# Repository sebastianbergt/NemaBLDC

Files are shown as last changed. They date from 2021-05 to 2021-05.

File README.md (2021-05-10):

# NemaBLDC

# Goal

Provide a Nema34 compatible case for C6374 170KV BLDC Motor with CUI AMT V102 encoder to be used as a powerful servo with [odrive](https://odriverobotics.com/).

# Pictures 

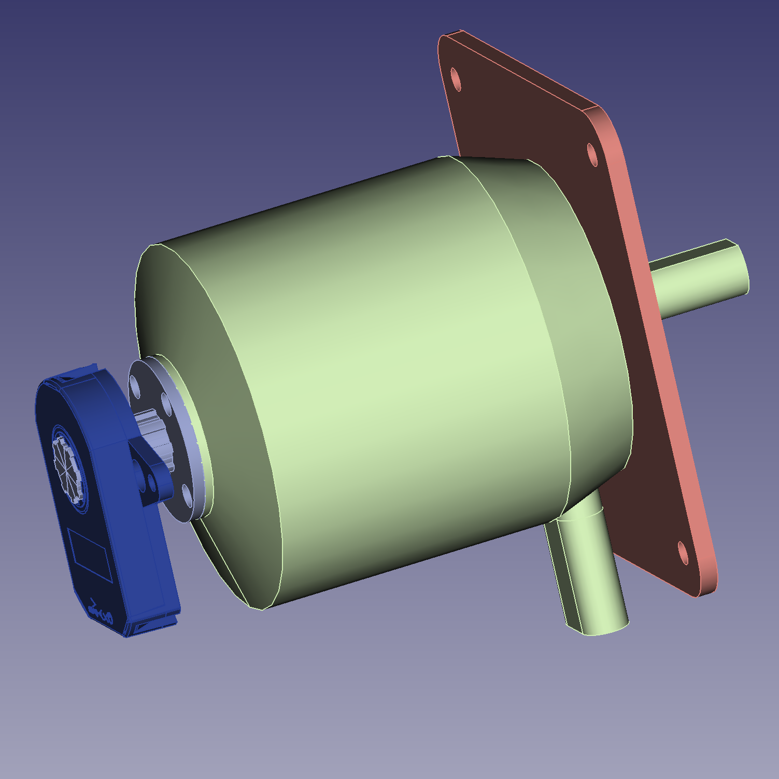
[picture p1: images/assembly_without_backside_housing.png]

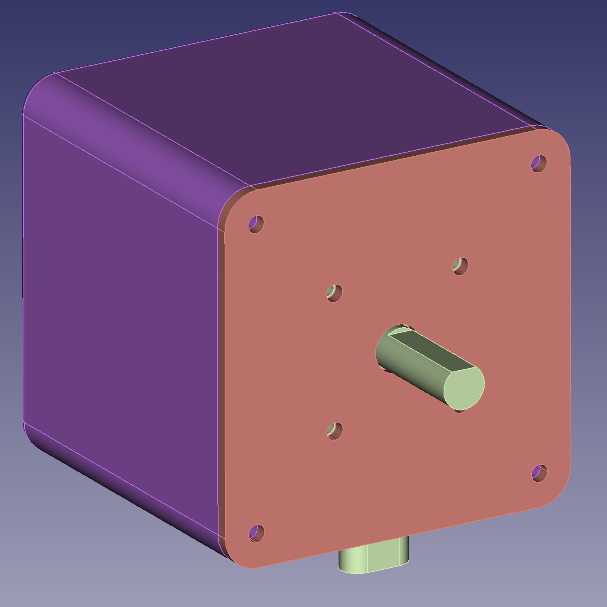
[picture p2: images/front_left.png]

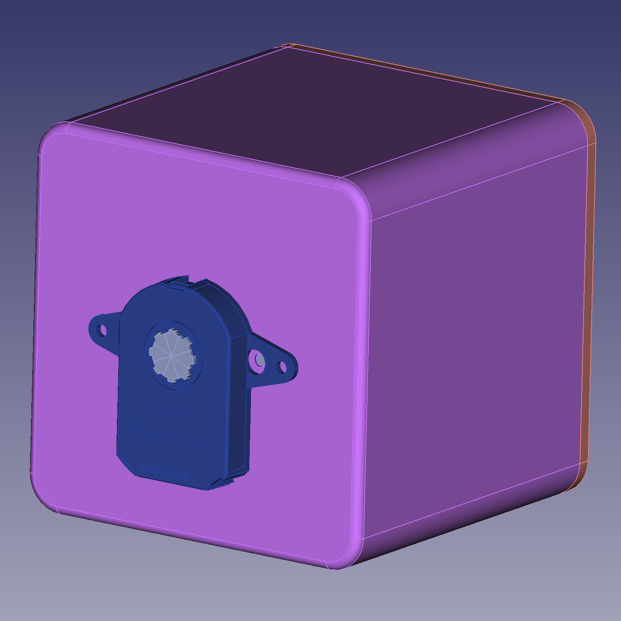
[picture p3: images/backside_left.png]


# Print

All parts were printed on [Prusa MK3S](https://www.prusa3d.com/) with PETG 0.15mm layer height and PrusaSlicer-2.2.0 default-QUALITY setting, 0.4mm nozzle as well as 2 perimeters without supports.
Back and front have 15% gyroid infill.
The encoder shaft has 100% rectolinear infill.
CAD were designed in freecad version 0.19 with Assembly 4 addon.

# Build

1. Clean the M4 nut slots as overhanging arches tend to produce a small amount of blocking material.
2. Insert M3 nuts and use tape or glue to hold them in place. 
3. Insert M4 nuts and use tape or glue to hold them in place.
4. Attach encoder mount, usually no need for using the mounting tool delivered with the encoder
5. Attach encoder and encoder cable
6. Attach encoder shaft to motor with 2 M4 screws
7. Attach motor to front plate with 4 M4 screws
8. Carefully insert motor into case, having the teeth of the encoder shaft visible to avoid damaging the shaft or the encoder.
9. Close the case with 4 M4 screws from the front.

# BOM

|Count |Part  | Comment
--- | --- | ---
|2|M3 nut|for the encoder mount
|2|M3 5mm screw|for the encoder mount
|4|M4 nut|
|10|M4 10mm screw|for motor and encoder shaft mounting and keeping the front on the box
|1|[AMT102-V](https://octopart.com/amt102-v-cui+devices-106233269)|
|1|[AMT102-V cable](https://octopart.com/search?q=CUI-3132-1FT&currency=USD&specs=0)|
|some|PETG filament|

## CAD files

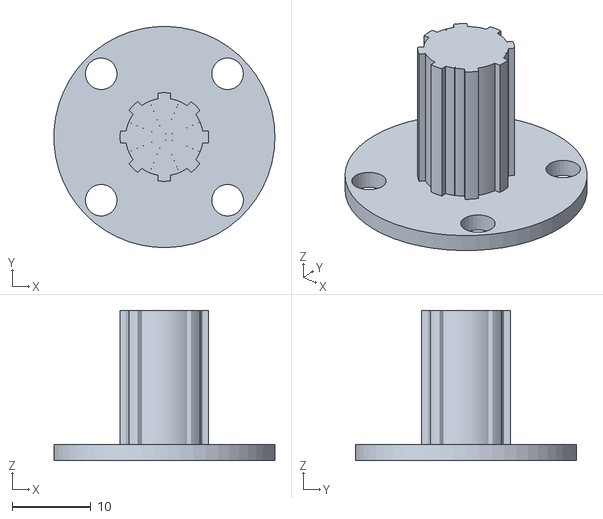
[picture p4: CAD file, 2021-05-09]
exports/Encoder_Shaft_Adapter-Encoder_Shaft_Adapter_v0.stl
28.0 x 28.0 x 19.0

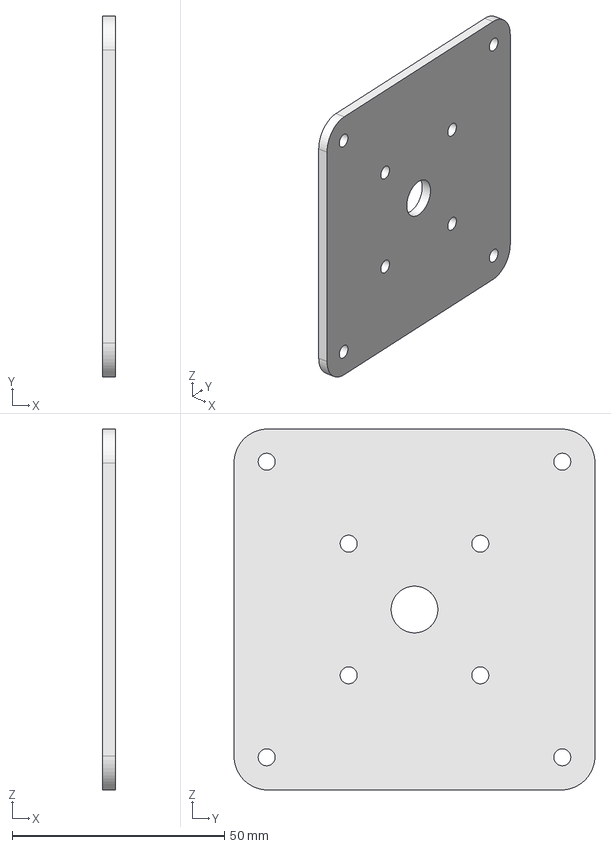
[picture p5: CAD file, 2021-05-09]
Motor_Housing_FrontPlate.FCStd
3.00 x 85.0 x 85.0 mm

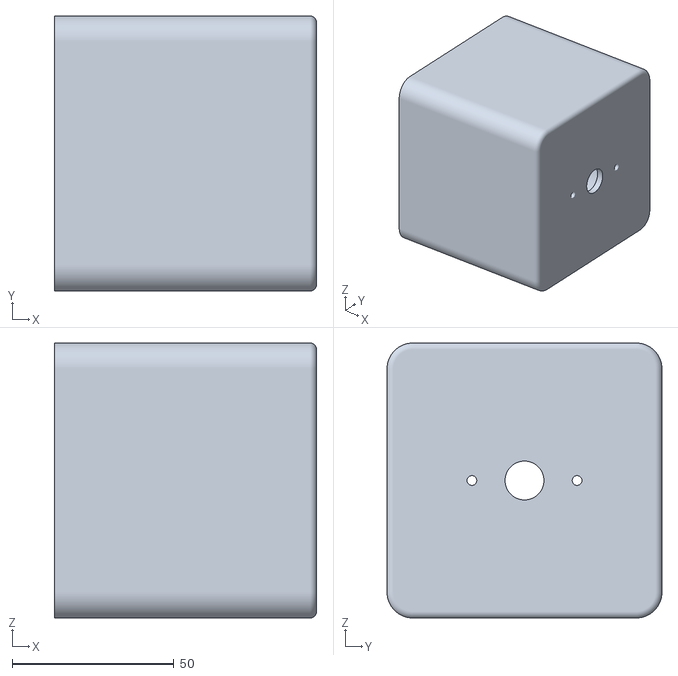
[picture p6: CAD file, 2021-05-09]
exports/Motor_Housing_Back-Motor_Housing_Back_v0.stl
81.0 x 85.0 x 85.0

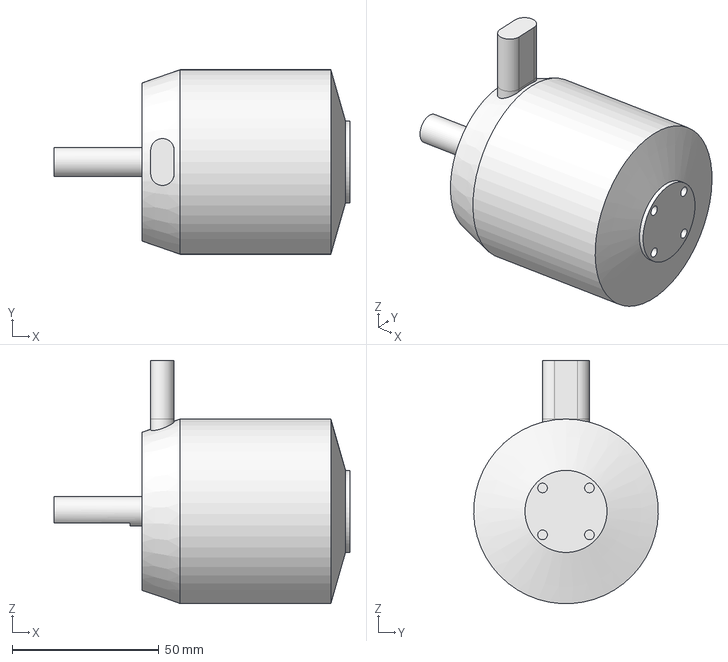
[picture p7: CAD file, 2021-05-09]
Motor_C6374_170KV.FCStd
101.0 x 63.0 x 82.9 mm

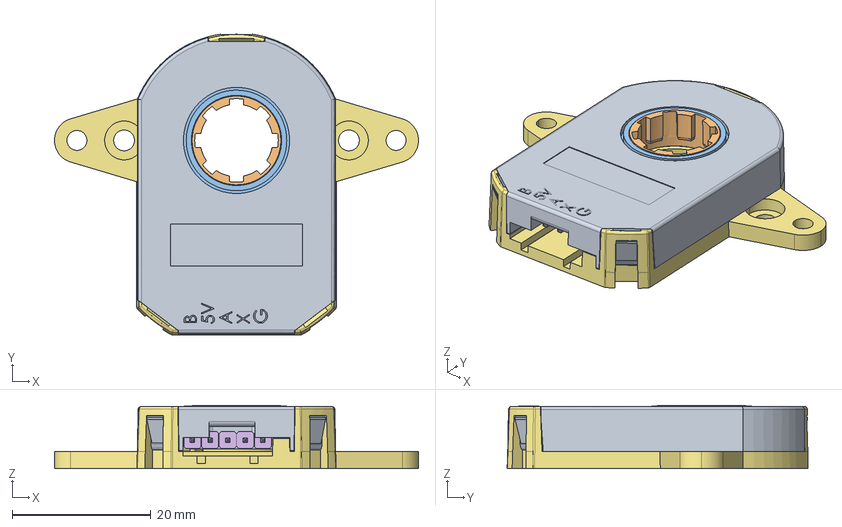
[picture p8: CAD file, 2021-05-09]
Encoder_AMT102V.FCStd
52.5 x 43.4 x 9.15 mm
CUI_DEVICES_AMT102_2048_I3000_W
CUI_DEVICES_AMT102_2048_I3000_W002
CUI_DEVICES_AMT102_2048_I3000_W003
CUI_DEVICES_AMT102_2048_I3000_W005
CUI_DEVICES_AMT102_2048_I3000_W006
CUI_DEVICES_AMT102_2048_I3000_W007
CUI_DEVICES_AMT102_2048_I3000_W008

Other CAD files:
Assembly_NemaBLDC.FCStd
exports/Motor_Housing_FrontPlate-Motor_Housing_FrontPlate_v0.stl
Motor_Housing_Back.FCStd
Encoder_Shaft_Adapter.FCStd
